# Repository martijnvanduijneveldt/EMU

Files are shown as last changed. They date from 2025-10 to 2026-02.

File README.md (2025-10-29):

[][cc-by-nc-sa]

# EMU – Expandable Multi-material Unit
### A new take on a MMU by <a href="https://github.com/DW-Tas">DW-Tas</a> and <a href="https://github.com/igiannakas">igiannakas</a><br/>
<a href="https://ko-fi.com/O5O5OCC0K"> Ko-Fi</a>

> [!WARNING] 
> ***Under Active/Early Development*** <br/>
> Build at your own risk

**Introducing the EMU, the Expandable Multi-material Unit from down under.** The EMU is a modular, flexible, upgradable, reliable and service-friendly MMU designed around the proven filamentalist V3 platform.

The EMU supports any number of lanes and base configurations; whether it is a **single lane setup** to assist filament loading, a **dual lane configuration** for endless spool, or a **multi-lane, multi base unit setup** for multi-material printing. It is also **expandable**, with no re-printing of parts required when upgrading from a 2 lane to a multiple lane setup.

<p align="center">
  
</p>

### Table of Contents
- [Design Objectives & Key Features](#design-objectives)
- [Render Gallery](#render-gallery)
- [Prints Gallery](#prints-gallery)
- [Documentation](/docs)
  - [BOM, Printing, Assembly and Wiring instructions](/docs/assembly_wiring)
  - [Software Setup and Calibration](/docs/software_setup)
  - [Slicer setup and optimisation for multi color prints](/docs/software_setup/05-slicer-setup.md)
- [License](#this-work-is-licensed-under-a)

### Highlights
- **Modular & Expandable** design, able to add lanes anytime and in any configuration. No reprints when upgrading from a 2 lane setup.
- **One screw or tool-free** access and servicing, even mid-print.
- **Sealed dry boxes** able to maintain humidity in the 15% range (with silica gel) or 5–8% range (with molecular sieves) for weeks.  
- **Humidity sensors** per lane for filament environmental monitoring.
- **Reliable endless spool** with no chance of the rewound filament interfering with neighbouring rolls.
- **Off-the-shelf electronics** (EBB42 with EBB36 also fully compatible).  
- **Per-lane controls** - eject button + LEDs.

<p align="center">
  
  
</p>

## Design Objectives

### Modularity & Upgradeability  
Each lane is fully self-contained, so you can choose **exactly how many lanes you need and group them as you like**. You can also **mix and match** lanes across multiple base units, or use a stand-alone single lane for extruder loading and print assistance. 

Expanding later is also straightforward. Just print lane expanders for the base and add another dry box assembly. There is no need to reprint or replace existing parts when upgrading from a 2 lane base. 

### Ease of Servicing 
All electrical and mechanical components are either **one screw or completely tool-free and immediately accessible**, making live troubleshooting possible even during a print. 

Access to the electronics is easy - just lift the dry box off its base for full access. The stepper tensioning screw is accessible without any dissassembly allowing on the fly tuning of filament grip. Finally, removing the filamentalist, stepper and stepper assembly is possible via one screw.

### Sealed Dry Boxes  
Each spool sits in its own purpose built, **fully sealed dry box with an integrated desiccant holder**. The boxes use foam cord in areas of potential air ingress to create a tight seal, with the clear 1.5mm PETG/PC panel also offering visibility inside the dry box.

The dry boxes can maintain humidity in the 15% range (with silica gel) or 5–8% range (with molecular sieves) for weeks. Finally, as each dry box is self contained, opening one to reload filament, doesn’t disturb its neighbours, extending the effective desiccant life.

<p align="center">
  
</p>

### Integrated Humidity Sensors 
Each lane monitors its own environment, letting you know when it’s **time to refresh the desiccant**. The humidity sensors are integrated into Mainsail (and optionally in Home Assistant for historical data tracking via the mainsail HA integration).

### Endless Spool Reliability
Dual pre-stepper sensors ensure **consistent run-out detection** and reliable re-wind, as the filament is always gripped by the stepper hobbed gear assembly. 

In addition, the isolated boxes ensure that any left over, rewound, filament cannot interfere with neighbouring lanes, **preventing a jam**.

### Built on the Filamentalist
The lane assembly is based on the proven **[filamentalist V3 design with 688 bearings](https://github.com/Enraged-Rabbit-Community/ERCF_v2/tree/master/Recommended_Options/Filamentalist_Rewinder/Filamentalist_FV3_Rewinder)**, with no modifications necessary. 
- Existing 688 bearing version filamentalist parts can be reused when building an EMU.
- Optionally, the revised tensioner mount further improves pre-stepper switch actuation.
- Wide spool size compatibility - built on the 74mm filamentalist stock setup and fits even KVP filament spools.

<p align="center">
  
  
</p>

### Integrated Filament Driving Stepper 
Each lane has its own driving stepper inside the dry box, resulting in a compact, **fully self-contained mechanical design**. In case of mechanical issue, you can swap out filamentalist assemblies with 3 screws, unplugging 2 JST plugs and unplugging the bowden tube. 

In addition, you can **swap out complete dry boxes** by unplugging two JST plugs and the bowden tube. This is helpful if you want to maintain a particularly moisture sensitive filament undisturbed when swapping it out from the EMU.

### Simple Electronics
The recommended BOM uses **readily available EBB42 boards** (with EBB36 fully compatible). MMB v2 boards can also be reused, though without humidity sensing due to I²C limitations and a slightly more intricate wiring.

In addition, **each lane has its own ventilation fan**, ensuring the stepper drivers do not overheat, even when the unit is placed on top of a hot printer. With the EBB42 and EBB36, the ventilation fans can also be speed controlled to minimize noise.

### Easy mounting
The EMU base assembly can be securely **mounted on extrusions** or using **rubber feet** directly on the printer or besides it. In either case the **electronics remain accessible** without needing to remove the unit from its mounts.

### Per-lane Controls  
Each lane includes its own eject button, status LED, and a filament colour LED that illuminates the dry box. 

## Render Gallery
<p align="center">
  
  
</p>
<p align="center">
  
  
</p>
<br/>

## Prints Gallery
<p align="center">
  1 (4)
  1 (5)
  1 (2)
  1 (3)
</p>

## This work is licensed under a
[Creative Commons Attribution-NonCommercial-ShareAlike 4.0 International License][cc-by-nc-sa].

[][cc-by-nc-sa]

[cc-by-nc-sa]: http://creativecommons.org/licenses/by-nc-sa/4.0/
[cc-by-nc-sa-image]: https://licensebuttons.net/l/by-nc-sa/4.0/88x31.png
[cc-by-nc-sa-shield]: https://img.shields.io/badge/License-CC%20BY--NC--SA%204.0-lightgrey.svg

## License clarification regarding non-commercial use:
The non-commercial aspect of this license is for cases where EMU is the product, not the use of EMU to create products.<br/>
I.e. If you wish to sell EMU as a product, you would need to seek a commercial license before doing so. </br>
It is NOT intended to prevent the use of EMU with a printer that you use to provide commercial services. If you want to run EMU in your print farm, go right ahead.

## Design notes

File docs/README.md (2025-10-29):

[][cc-by-nc-sa]

# EMU – Expandable Multi-material Unit Documentation
### A new take on a MMU by <a href="https://github.com/DW-Tas">DW-Tas</a> and <a href="https://github.com/igiannakas">igiannakas</a><br/>
<a href="https://ko-fi.com/O5O5OCC0K"> Ko-Fi</a>

## Step 1: [Printing, assembly and wiring](/docs/assembly_wiring)
This page explains the EMU assembly and wiring. It links the BOM, detailed print settings for all of the EMU parts, including tips on how to achieve the optimal print reseults. It also includes the assembly videos, covers multi-lane and single-lane wiring for both EBB42/36 boards.

- [BOM](/docs/assembly_wiring/#bom)
- [Print Settings](/docs/assembly_wiring/#print-settings)
  - [Filamentalist components and Lane stepper components](/docs/assembly_wiring/#filamentalist-components-and-lane-stepper-components)
  - [Dry Box components](/docs/assembly_wiring/#dry-box-components)
  - [Base unit components](/docs/assembly_wiring/#base-unit-components)
- [Assembly Videos](/docs/assembly_wiring/#assembly-videos)
  - [Part 1: Filamentalist and Stepper Assembly Guide](/docs/assembly_wiring/#part-1-filamentalist-and-stepper-assembly-guide)
  - [Part 2: Drybox Assembly Guide](/docs/assembly_wiring/#part-2-drybox-assembly-guide)
  - [Part 3: Base Assembly Guide](/docs/assembly_wiring/#part-3-base-assembly-guide)
  - [Part 4: Electronics Assembly Guide](/docs/assembly_wiring/#part-3-base-assembly-guide)
- [Wiring Instructions and Diagrams](/docs/assembly_wiring/#wiring-instructions-and-diagrams)

## Step 2: [EMU board setup](/docs/software_setup/01-board-setup.md)
This page explains in detail how to setup your EMU boards with CANBus, how to flash Katapult and klipper as well as the procedure to update the klipper firmware.

- [Setting up CAN Bus](/docs/software_setup/01-board-setup.md#setting-up-can-bus)
- [Flashing the EBB boards](/docs/software_setup/01-board-setup.md#flashing-the-ebb-boards)
- [Updating the boards with the latest klipper version](/docs/software_setup/01-board-setup.md#updating-the-boards-with-the-latest-klipper-version)

## Step 3: [Happy Hare setup](/docs/software_setup/02-happy-hare-setup.md)
This page explains the step by step process to install and set up Happy Hare, the MMU management software that drives the EMU.

- [Installing Happy Hare](/docs/software_setup/02-happy-hare-setup.md#installing-happy-hare)
- [Configuring the EMU hardware](/docs/software_setup/02-happy-hare-setup.md#configuring-the-emu-hardware)
- [Configuring Happy Hare parameters](/docs/software_setup/02-happy-hare-setup.md#configuring-happy-hare-parameters)
      
## Step 4: [Calibration and startup](/docs/software_setup/03-calibration-and-startup.md)
This page explains the step by step process to calibrate the unit and the initial start up checks required to ensure successful first operation.

- [Lane rotation distance calibration](/docs/software_setup/03-calibration-and-startup.md#lane-rotation-distance-calibration)
- [Bowden tube calibration](/docs/software_setup/03-calibration-and-startup.md#bowden-tube-calibration)
- [First start up](/docs/software_setup/03-calibration-and-startup.md#first-start-up)

## Step 5: [Slicer setup and optimisation for multi color prints](/docs/software_setup/05-slicer-setup.md)
Describes the mangatory Orca slicer setup required for single extruder multi-material printing, including print profile settings to achieve optimal quality results.

- [Orca slicer mandatory setup](/docs/software_setup/05-slicer-setup.md#orca-slicer-mandatory-setup)
- [Orca slicer profile tuning for multi-color printing](/docs/software_setup/05-slicer-setup.md#orca-slicer-profile-tuning-for-multi-color-printing)

## Next steps
Once you have completed the guide above you should have a fully functioning EMU unit! Optionally you can also set up:
1. Klipper screen integration: https://github.com/moggieuk/Happy-Hare/wiki/KlipperScreen
2. Mainsail / Fluid MMU panel: https://github.com/moggieuk/Happy-Hare/wiki/Mainsail-Fluidd-Integration
3. Spoolman: https://github.com/moggieuk/Happy-Hare/wiki/Spoolman-Support

In addition, to add further lanes, follow  the instructions here: [Expanding the unit](/docs/software_setup/04-expanding-the-unit.md)

## Seeking help

The Happy Hare discord is a great resource to help you going. Both in the general channel as well as the dedicated EMU channel. Link to the discord can be found here: https://discord.gg/aABQUjkZPk

<p align="center">
  
</p>

#### This work is licensed under a
[Creative Commons Attribution-NonCommercial-ShareAlike 4.0 International License][cc-by-nc-sa].

[][cc-by-nc-sa]

[cc-by-nc-sa]: http://creativecommons.org/licenses/by-nc-sa/4.0/
[cc-by-nc-sa-image]: https://licensebuttons.net/l/by-nc-sa/4.0/88x31.png
[cc-by-nc-sa-shield]: https://img.shields.io/badge/License-CC%20BY--NC--SA%204.0-lightgrey.svg

### License clarification regarding non-commercial use:
The non-commercial aspect of this license is for cases where EMU is the product, not the use of EMU to create products.<br/>
I.e. If you wish to sell EMU as a product, you would need to seek a commercial license before doing so. </br>
It is NOT intended to prevent the use of EMU with a printer that you use to provide commercial services. If you want to run EMU in your print farm, go right ahead.

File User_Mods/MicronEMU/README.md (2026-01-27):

# Micron EMU hat

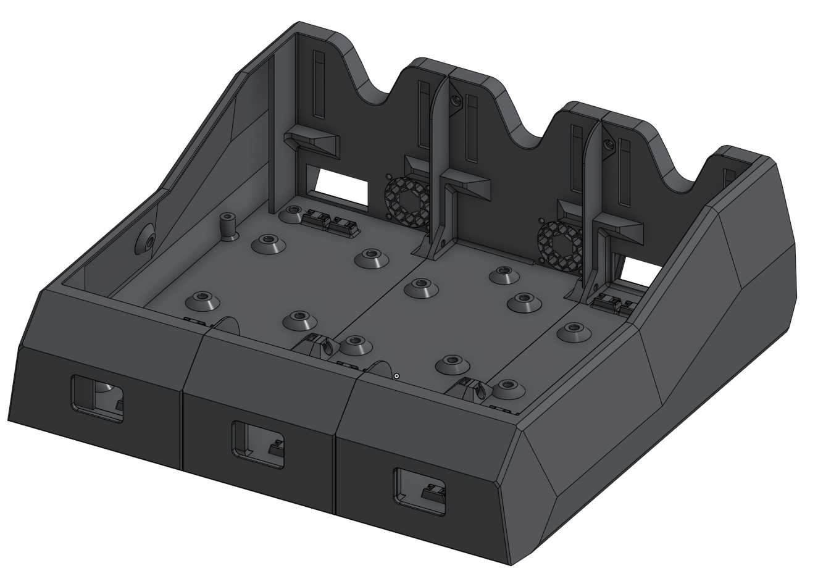
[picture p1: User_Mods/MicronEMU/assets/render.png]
a CAD render of the Micron EMU bases


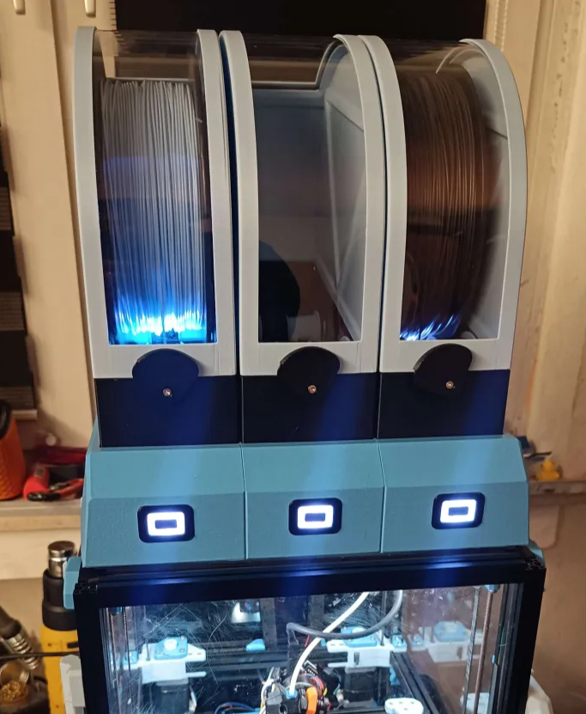
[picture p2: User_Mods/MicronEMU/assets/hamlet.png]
a photograph of the Micron EMU base in light blue on top of M.211 "Hamlet"


This mod replaces the base units to fit three boxes onto a Micron in *stealth* aesthetic. It mounts to the top extrusions using four screws, requiring post-loading of two nuts per front-to-back top extrusion.

Print using upstream settings, including painting fuzzy skin.

## Acknowledgements

Many thanks to @hartk for providing the rough-cut of the Micron EMU base. @burkfers cut the button holes, did diverse polishing, and tested.

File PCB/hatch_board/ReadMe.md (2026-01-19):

## EMU Wiring Hatch Board

The **EMU Wiring Hatch Board** is a dedicated PCB designed for EMU to make wiring and assembly easier and more convenient. It replaces the printed hatch ([Box_wiring_hatch](https://github.com/DW-Tas/EMU/blob/main/STL/Box/%5Ba%5D_Box_wiring_hatch.stl)), eliminates the need to solder the Filamentalist assembly wires to the JST connectors, and removes the need to use silicone to seal gaps around the JST connector.

The EMU Wiring Hatch Board was designed and developed by <a href="https://github.com/kashine6">kashine6</a>.

## Key Features

1. **Eliminates the need to solder wires directly to JST connectors**
   - Simplifies assembly
   - Reduces soldering complexity
   - Improves maintainability, as the Filamentalist assembly can be easily unplugged from inside the base unit

2. **Simplified pre-stepper sensor connections**
   - The two pre-stepper switches no longer need to be soldered in parallel. Instead, solder the sensor and ground wires to each switch individually, then plug them into the board separately.

3. **Easier box sealing**
   - Removes the need to use silicone to seal the JST connector on the hatch cover.

4. **Wire labeling**
   - Wire labels on the PCB silkscreen reduce the chance of wiring errors during assembly.



## BOM variations vs. baseline EMU BOM
Due to the PCB being thinner than the printed box wiring hatch, **the 2x M3x8mm FHCS screws are now replaced by 2x M3x6 BHCS/SHCS screws**.

If buying pre-assembled, the corresponding straight through hole PCB header JST connectors in the BOM are no longer needed (1x JST XH 8 pin plug and 1x JST XH 4 pin plug).

If making your own and soldering the JST headers, you'll need the below additions:
- 3x JST XH Series Straight Through Hole PCB Header, 4 Contact
- 3x JST XH Series Straight Through Hole PCB Header, 2 Contact 

## This work is licensed under a
[Creative Commons Attribution-NonCommercial-ShareAlike 4.0 International License][cc-by-nc-sa].

[][cc-by-nc-sa]

[cc-by-nc-sa]: http://creativecommons.org/licenses/by-nc-sa/4.0/
[cc-by-nc-sa-image]: https://licensebuttons.net/l/by-nc-sa/4.0/88x31.png
[cc-by-nc-sa-shield]: https://img.shields.io/badge/License-CC%20BY--NC--SA%204.0-lightgrey.svg

## License clarification regarding non-commercial use:
The non-commercial aspect of this license is for cases where EMU is the product, not the use of EMU to create products.<br/>
I.e. If you wish to sell EMU as a product, you would need to seek a commercial license before doing so. </br>
It is NOT intended to prevent the use of EMU with a printer that you use to provide commercial services. If you want to run EMU in your print farm, go right ahead.

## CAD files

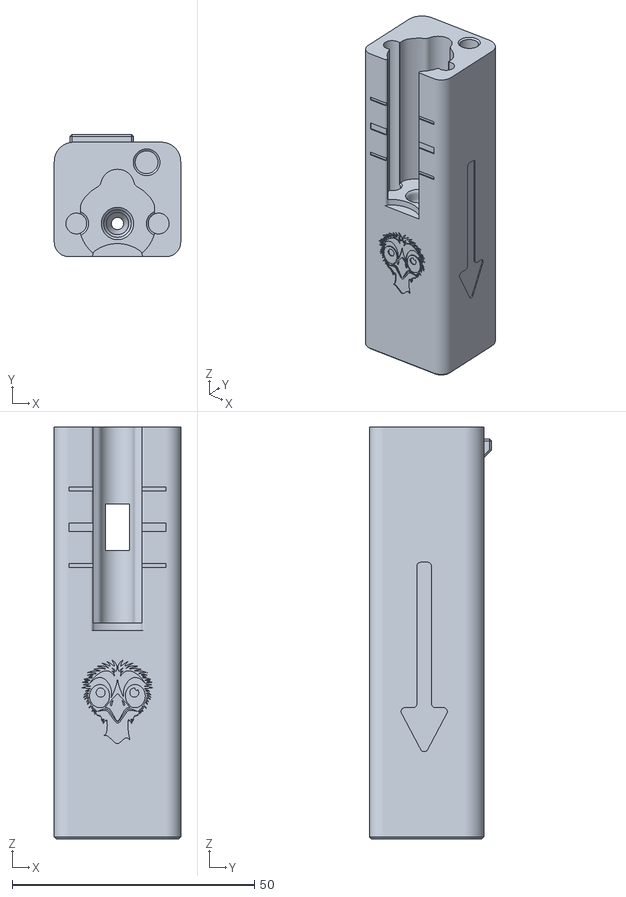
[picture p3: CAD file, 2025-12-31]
STL/Tension-compression-sensor/Proportional Sync Feedback (PSF) Version/EMUSync_main_body[PSF].stl
26.1 x 25.2 x 85.0

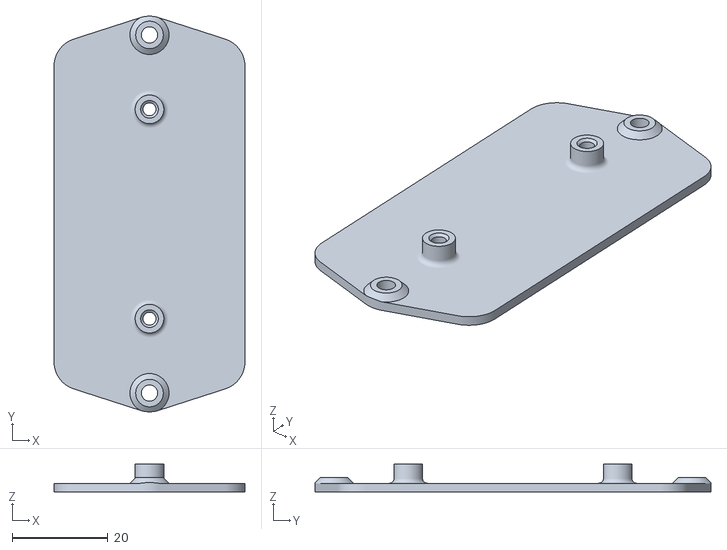
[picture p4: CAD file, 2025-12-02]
STL/Base/[a]_Ebb36_Mount.stl
40.0 x 82.9 x 5.80

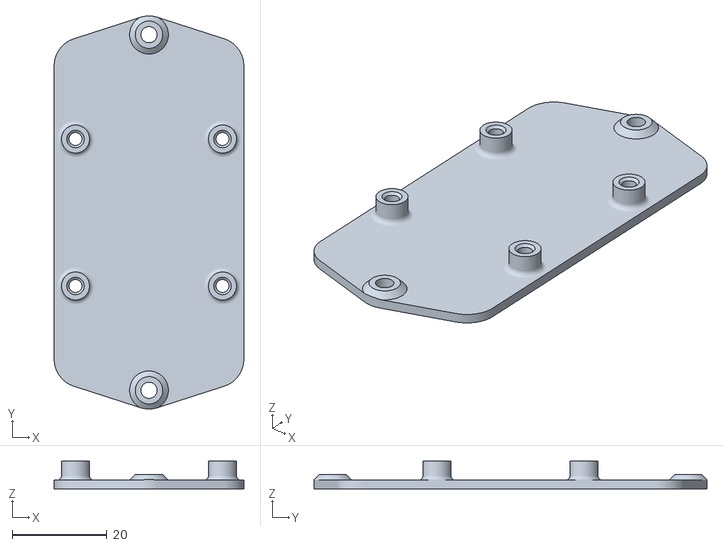
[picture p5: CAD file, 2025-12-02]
STL/Base/[a]_Ebb42_Mount.stl
40.0 x 82.9 x 5.80

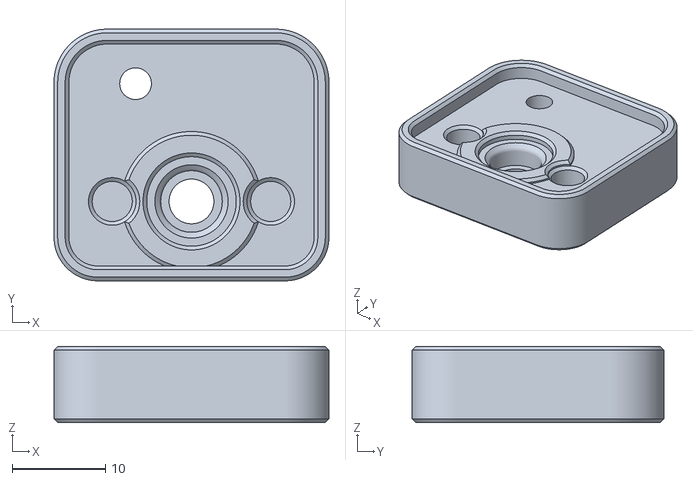
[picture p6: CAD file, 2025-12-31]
STL/Tension-compression-sensor/Proportional Sync Feedback (PSF) Version/[a]_End_cap[PSF].stl
29.5 x 27.0 x 8.20

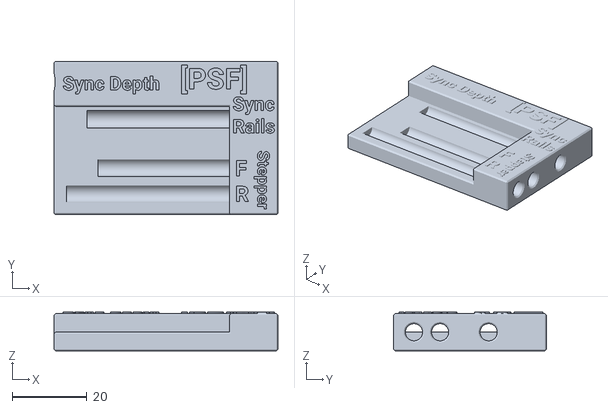
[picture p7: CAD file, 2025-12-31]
STL/Tension-compression-sensor/Proportional Sync Feedback (PSF) Version/PTFE Cutter and Length Tool[PSF].stl
60.0 x 41.0 x 10.4

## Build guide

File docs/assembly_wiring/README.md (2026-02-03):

# EMU - BOM, Printing, Assembly and Wiring Guide

## Table of Contents
- [BOM](#bom)
- [Print Settings](#print-settings)
  - [Filamentalist components and Lane stepper components](#filamentalist-components-and-lane-stepper-components)
  - [Dry Box components](#dry-box-components)
  - [Base unit components](#base-unit-components)
- [Assembly Videos](#assembly-videos)
  - [Part 1: Filamentalist and Stepper Assembly Guide](#part-1-filamentalist-and-stepper-assembly-guide)
  - [Part 2: Drybox Assembly Guide](#part-2-drybox-assembly-guide)
  - [Part 3: Base Assembly Guide](#part-3-base-assembly-guide)
  - [Part 4: Electronics Assembly Guide](#part-3-base-assembly-guide)
  - [Part 5: EMU Sync Assembly images](#part-5-emu-sync-assembly-images)
- [Wiring Instructions and Diagrams](#wiring-instructions-and-diagrams)
- [Wiring key dimensions](#wiring-key-dimensions)
  - [Base wiring dimensions](#base-wiring-dimensions)
  - [PCB Hatch wiring dimensions](#pcb-hatch-wiring-dimensions)
  - [DIY Hatch (no pcb) wiring dimensions](#diy-hatch-no-pcb-wiring-dimensions)

<p align="center">
  
</p>

## BOM  
The EMU Bill of Materials can be found here: [Draft BOM](https://docs.google.com/spreadsheets/d/1jYJXBgpc_iLDfC17fC2LTYKrSEy5ocPbGEQ_EEOGCvI)

**Recommended optional extras:**
1. [PCB hatch boards](https://github.com/DW-Tas/EMU/tree/main/PCB/hatch_board) - simplifies wiring.
2. [Proportional Sync Feedback Sensor](https://www.aliexpress.com/item/1005010470743517.html) - allows for clog, tangle detection and more accurate syncronisation between the EMU and the extruder.

## Print Settings

### Filamentalist components and Lane stepper components:
The below print settings are recommended for the filamentalist and lane stepper components. These are structural parts hence require print settings optimised for strength:
- 0.2 mm layer height
- 0.2 mm first layer height
- 4 walls
- 40% infill
- 0.4mm extrusion width (line width) throughout
- Gyroid sparse infill is recommended as it tends to warp less
- Inner Outer wall ordering, to ensure overhangs and supported areas do not sag
- Arachne wall generator
- One wall top and bottom surfaces (optional but recommended - parts look nicer)
- Disable thick bridges
- Z hop enabled to avoid nozzle scraping (0.2 is sufficient)

> [!IMPORTANT]
> **Parts are not shrinkage compensated** - calibrate your filament shrinkage first! If the bearings are loose, you're either under extruding, or over compensating for shrinkage.<br/>
> **Disable thick bridges** in your slicer and make sure your flow rate (EM) is on point! **Over extrusion, thick bridges and insufficient cooling will cause your sensor magnets and bearings not to fit as the bridges will sag.**

**For the TPU filamentalist CDR ring:**
- 0.2 mm layer height
- 0.2 mm first layer height
- 0.4mm extrusion width (line width) throughout
- 6 walls, so that the object is printed solid
- Avoid crossing walls enabled
- Random seam. This is important to avoid an aligned seam bump
- Inner Outer wall ordering, to ensure overhangs and supported areas do not sag
- Z Hop turned off to reduce stringing
  
> [!IMPORTANT]
> Printing TPU can be a challenge - print by object and a slight negative (-0.1) extra length on retract can help reduce stringing.

### Dry Box components:
The below print settings are recommended for the dry boxes and the desiccant holder. The dry boxes need to be as air tight as possible, hence the recommended print settings below are tuned to achieve this while keeping filament use under control.
- 0.2 mm layer height
- 0.2 mm first layer height
- 3 walls
- 15% infill
- For the lid specifically, use 4 walls and 30% infill to ensure strength in the front lip.
- 0.4mm extrusion width (line width) throughout
- Gyroid sparse infill is recommended as it tends to warp less
- Inner Outer wall ordering, to ensure dry box hatch features print with minimal sagging.
- Arachne wall generator
- One wall top and bottom surfaces (optional but recommended - parts look nicer)
- Disable thick bridges
- Z hop enabled to avoid nozzle scraping (0.2 is sufficient)

> [!IMPORTANT]
> Print with **extra first layer squish, use an adhesion promoter on the bed and in a pre-heated chamber with low fan** to prevent warping and ensure better layer adhesion. Mouse ears on the box corners may be required. Slight lifting will not impact part function.<br/>
> **Do not use mouse ears on the lid** as the slicer wrongly fills in the aesthetic lines.<br/>
> **Over extrude (only) the box and lid by ~2% (0.02)** to ensure air tightness. Increase your slicer flow multiplier (EM) by 0.02.

### Base unit components:
The below print settings are recommended for the base units and their accessories. 
- 0.2 mm layer height
- 0.2 mm first layer height
- 3 walls
- 15% infill
- 0.4mm extrusion width (line width) throughout
- Gyroid sparse infill is recommended as it tends to warp less
- Inner Outer Inner wall ordering to improve visual appearance
- Arachne wall generator
- One wall top and bottom surfaces (optional but recommended - parts look nicer)
- Disable thick bridges
- Z hop enabled to avoid nozzle scraping (0.2 is sufficient)
- For the **Eject button lens, 99 walls are recommended,** to reduce possibility of infill shining through the natural ABS

> [!IMPORTANT]
> Print with **extra first layer squish, use an adhesion promoter on the bed and in a pre-heated chamber with low fan** to prevent warping. Slight lifting will not impact part function.

> [!NOTE]
> **Paint on fuzzy skin** on the outer walls of the base unit will improve appearance.<br/>
> Paint on ONLY, not full model fuzzy skin. <br/>
> 0.1 distance, 0.1 or 0.2mm depth. Displacement method (orca slicer)

## Assembly Videos

### Part 1: Filamentalist and Stepper Assembly Guide
EMU Filamentalist and Stepper Assembly Guide (https://www.youtube.com/watch?v=FNcXC9HXUmI)
<br/>
**Errata:**
1. BMG Gear insertion is not visible in the video. Do this before adding the stepper main body and screwing it on.
2. Switch sensor screws are M2x10 self taping or m2x8 bhcs/shcs
3. Filament path - BMG gear alignment step is not shown in the video. Insert some filament through the unit manually, loosen the BMG gear set screw and move it back and forth. Screw down the BMG gear.
4. For the BMG tensioning arm, the bushing is no longer an option. 
5. Add a washer to the stepper tensioning arm on both sides of the spring.
6. Stepper body screws are all M3x20
7. Front ECAS is no longer required
8. PTFE tube lengths have been updated since the video release. [Use the dedicated cutter STL](https://github.com/DW-Tas/EMU/blob/main/STL/Tools/PTFE%20Cutter%20and%20Length%20Tool.stl) to measure and cut the PTFE tubes.

### Part 2: Drybox Assembly Guide
EMU Dry Box Assembly Guide (https://www.youtube.com/watch?v=JZzMyOBCdSM)
<br/>

**Errata:**
1. A threaded stand off is inserted in the front lip of the lid and secured from either side with M3x40 FHCS bolts.
2. Box and wiring hatch changes - the wiring hatch now is screwed in from the outside of the unit. Push through the hole from the inside out and then screw in place.
3. Wiring hatch foam is now glued on the box itself. The foam chord channel is on the outside of the box. 
4. The BME sensor has been relocated to the LED cover.

### Part 3: Base Assembly Guide
EMU Base Assembly Guide (https://www.youtube.com/watch?v=2SmAMuXas38)
<br/>

### Part 4: Electronics Assembly Guide
EMU Elecrronics Assembly Guide (https://www.youtube.com/watch?v=Iang2JYkTh8)
<br/>

**Errata:**
1. Base unit top clamping screws (M3x8 FHCS) now screw into heatset inserts inserted on the other side of the frame.
2. External combiner sensor is no longer specified in the default setup. That wiring part can be omitted.
3. Encoder is no longer specified in the default setup. That wiring part can be omitted.

### Part 5: EMU Sync Assembly images
<table>
  <tr>
    <td>Step 1</td>
    <td>Step 2</td>
    <td>Step 3</td>
  </tr>
  <tr>
    <td>Step 4</td>
    <td>Step 5</td>
    <td>Step 6</td>
  </tr>
  <tr>
    <td>Step 7</td>
    <td>Step 8</td>
    <td>Step 9</td>
  </tr>
  <tr>
    <td>Step 10</td>
    <td>Step 11</td>
    <td>Step 12</td>
  </tr>
  <tr>
    <td>Step 13</td>
    <td>Step 14</td>
    <td>Step 15</td>
  </tr>
</table>

### Combiner:
Make sure the PTFE tube is pushed all the way inside the combiner. Not just at the ecas entry!



## Wiring Instructions and Diagrams
Depending on the number of lanes assembled, the wiring will vary slightly. Below are some initial wiring key notes to get your started.<br/>

**Multi-lane setup wiring notes (2+ lanes)**
1. Please note that the sync feedback sensor is connected to the first lane board. The encoder and combiner endstop is connected to the second lane EBB board.
2. The CAN bus umbilical from the printer feeds power and the CAN H / L wires to the WAGO connectors in the first lane. 
3. A 24V and Ground "bus" is established throughout the base unit using the two rearward WAGO connectors (WAGO 3 and WAGO 4).
4. The EBB boards connect to the power bus for power via their XT ports.
5. The EBB boards are daisy chained to establish the CANbus network. The first lane canbus High / Low / Power wires are connected to the first lane WAGO connectors.
7. The second lane canbus High / Low wires are connected to the CAN out dupont connectors on the first board itself. Creates the daisy chain
9. The last EBB board needs the 120Ohm resistor installed.
10. The second lane, third lane etc 2nd WAGO connector is used to connect the Neopixel Out wire from the eject button to the Neopixel In wire on the dry box.
11. The second lane, third lane etc 1st WAGO connector is used to connect the Neopixel Out wire from the dry box to the next lane Neopixel In wire on the eject button.

**Adding a second base unit** <br/>
You can daisy chain as many base units as you desire. Simply wire the XT30+2 CAN out port next to the last lane to the power bus and CAN H / L dupont connectors on the last EBB board. The next base unit can connect using a standard CAN Bus cable to the first unit.

**Single-lane setup wiring notes (2+ lanes)** <br/>
1. A single lane setup does not support an encoder/combiner. Instead, the Post Extruder sensor is configured in the Happy Hare configuration as the gate sensor.
2. There is no daisy chaining required. The single EBB board is connected to the first lane WAGO connectors.
3. There is no daisy chaining of subsequent lane Neopixels. 

**EBB 42 wiring diagram**<br/>
<p align="center">
  
</p>

**EBB 36 wiring diagram**<br/>
Please note, the EBB36 uses identical pin definitions to the EBB42.
<p align="center">
  
</p>

**Printer PSU**<br/>
> [!WARNING]
> You need to evaluate whether your PSU has enough power headroom. This entirely depends on your printer's overall setup. Ideally **plan for ~20 Watts for an 5 lane MMU** with **each additional lane requiring approximately an additional ~2-2.5 Watts.**

Key factors to consider:
1. PSU wattage
2. How many A-B/X-Y and Z steppers 
3. At what current the main printer steppers are operating at and what print speeds you operate them at
4. Your heater cartridge wattage 
5. What other power consuming accessories are connected to the printer (cpap, heater bed if 24V etc)

Depending on the combined power consumption, you may need to consider whether a PSU upgrade is needed. 

As a rule of thumb, a 12 lane EMU build with 4 Z steppers and 2 AB steppers running moderately high currents and high print speeds on a Voron 2.4 may require a 350Watt power supply to ensure adequate power headroom.

## Wiring key dimensions

This parts describes the recommended wire length for easy assembly and maintenance.

### Base wiring dimensions

<p align="center">
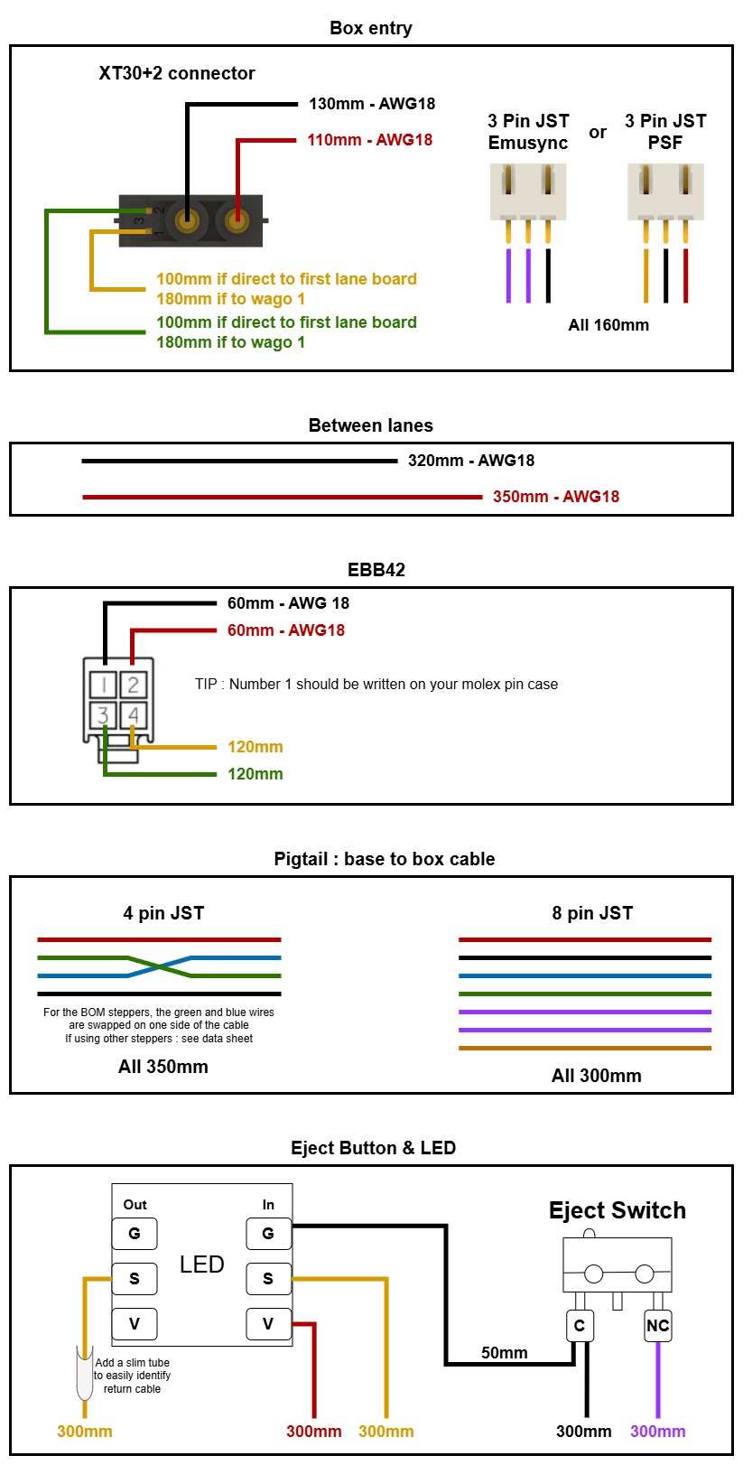
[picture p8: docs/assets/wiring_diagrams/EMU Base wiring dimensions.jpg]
  
</p>

### PCB Hatch wiring dimensions
> These dimensions are for the latest version of the PCB (Post sensor at the rear). If you have the older board (Post Sensor at the center) [refer to this image](../assets/wiring_diagrams/EMU%20PCB%20Hatch%20wiring%20dimensions%20-%20Old%20PCB.jpg) for sensor wire lengths.
<p align="center">
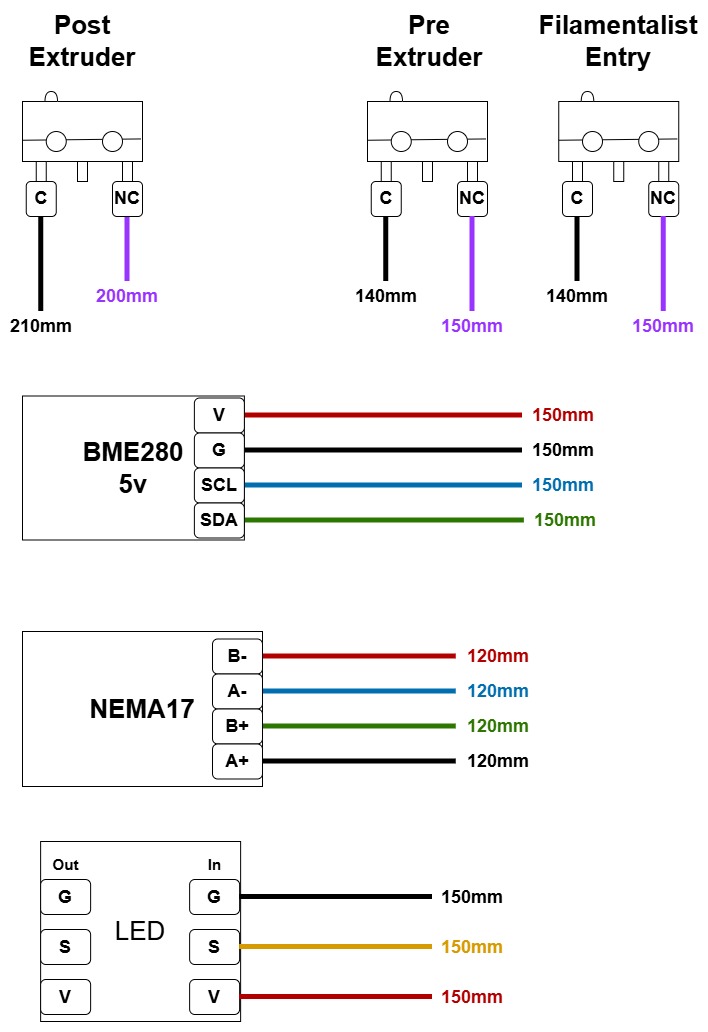
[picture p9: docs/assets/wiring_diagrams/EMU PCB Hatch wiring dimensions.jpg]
  
</p>

### DIY Hatch (no pcb) wiring dimensions

> These wiring dimensions assume you mount the BME sensor on the led cover and connect `5V` and `Ground` of the BME sensor to the led out `5V` and `Ground`.

<p align="center">
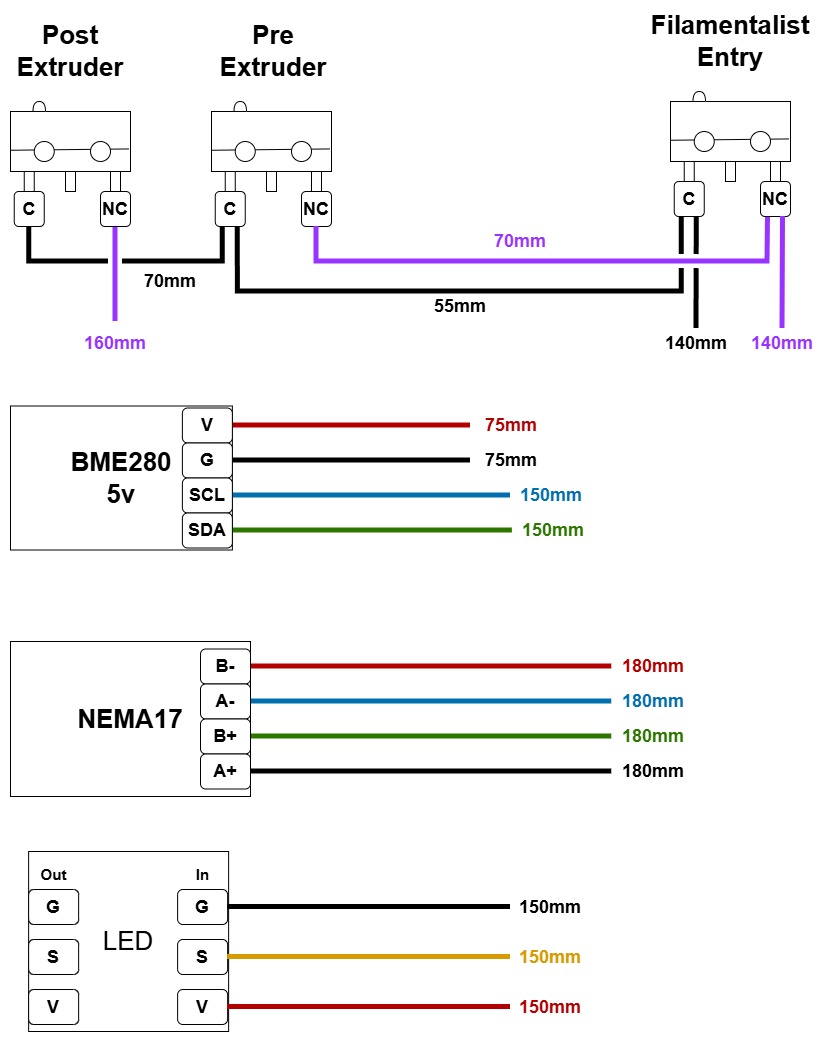
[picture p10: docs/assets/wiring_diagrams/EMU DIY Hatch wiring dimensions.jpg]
  
</p>

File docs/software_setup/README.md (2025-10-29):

# EMU Software Setup Guide

This is a provisional sofware setup guide for the EMU using Happy Hare v3. Happy Hare is an open-source filament changer controller for multi-color printing and is required for the EMU to function.

This guide is meant to be read in conjunction with the Happy Hare guides as found here: https://github.com/moggieuk/Happy-Hare/wiki and with Esoterical's CANBus setup guide as found here: https://canbus.esoterical.online. 

## Table of Contents

- [EMU board setup guide](/docs/software_setup/01-board-setup.md)
  - [Setting up CAN Bus](/docs/software_setup/01-board-setup.md#setting-up-can-bus)
  - [Flashing the EBB boards](/docs/software_setup/01-board-setup.md#flashing-the-ebb-boards)
  - [Updating the boards with the latest klipper version](/docs/software_setup/01-board-setup.md#updating-the-boards-with-the-latest-klipper-version)
- [Happy Hare setup guide](/docs/software_setup/02-happy-hare-setup.md)
  - [Installing Happy Hare](/docs/software_setup/02-happy-hare-setup.md#installing-happy-hare)
  - [Configuring the EMU hardware](/docs/software_setup/02-happy-hare-setup.md#configuring-the-emu-hardware)
  - [Configuring Happy Hare parameters](/docs/software_setup/02-happy-hare-setup.md#configuring-happy-hare-parameters)
- [Calibration and startup guide](/docs/software_setup/03-calibration-and-startup.md)
  - [Lane rotation distance calibration](/docs/software_setup/03-calibration-and-startup.md#lane-rotation-distance-calibration)
  - [Bowden tube calibration](/docs/software_setup/03-calibration-and-startup.md#bowden-tube-calibration)
  - [First start up](/docs/software_setup/03-calibration-and-startup.md#first-start-up)
- [Expanding the unit guide](/docs/software_setup/04-expanding-the-unit.md)
- [Slicer setup and optimisation for multi color prints](/docs/software_setup/05-slicer-setup.md)
  - [Orca slicer mandatory setup](/docs/software_setup/05-slicer-setup.md#orca-slicer-mandatory-setup)
  - [Orca slicer profile tuning for multi-color printing](/docs/software_setup/05-slicer-setup.md#orca-slicer-profile-tuning-for-multi-color-printing)

## Next Steps
Once you have completed the guide above you should have a fully functioning EMU unit! Optionally you can also set up:
1. Klipper screen integration: https://github.com/moggieuk/Happy-Hare/wiki/KlipperScreen
2. Mainsail / Fluid MMU panel: https://github.com/moggieuk/Happy-Hare/wiki/Mainsail-Fluidd-Integration
3. Spoolman: https://github.com/moggieuk/Happy-Hare/wiki/Spoolman-Support

## Seeking help

The Happy Hare discord is a great resource to help you going. Both in the general channel as well as the dedicated EMU channel. Link to the discord can be found here: https://discord.gg/aABQUjkZPk

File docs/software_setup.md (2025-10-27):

# EMU Happy Hare Hardware and Software Setup Guide

This is a provisional sofware setup guide for the EMU using Happy Hare v3. This guide is meant to be read in conjunction with the Happy Hare setup guide as found here: https://github.com/moggieuk/Happy-Hare/wiki

## Table of Contents

- [Setting up CAN Bus](#setting-up-can-bus)
- [Flashing the EBB boards](#flashing-the-ebb-boards)
- [Updating the boards with the latest klipper version](#updating-the-boards-with-the-latest-klipper-version)
- [Setting up Happy Hare](#setting-up-happy-hare)
- [Configuring the EMU hardware in Happy Hare](#configuring-the-emu-hardware-in-happy-hare)
- [Configuring Happy Hare](#configuring-happy-hare)
- [Calibrating the unit](#calibrating-the-unit)
- [First start up](#first-start-up)
- [Next steps](#next-steps)

## Setting up CAN Bus
If your printer does not have canbus set up, follow the excellent guide from Esoterical here: https://canbus.esoterical.online. If you are not familiar with CAN Bus, read through the guide from Esoterical. **CAN Bus is simple to set up and operate, but please do read the guide to familiarise yourselves with the CAN Bus concepts and terminology.**

Do not forget to terminate the last EBB board or CANBus device in your bus (depending on your bus topology).

## Flashing the EBB boards
Prior to setting up the EMU, the EBB boards need to be flashed with Katapult and Klipper. Flashing instructions can be found here https://canbus.esoterical.online/toolhead_flashing.html. The boards are flashed in exactly the same way as if they were used as a toolhead board. Below are some high level instructions; however do refer back to the guide by Esoterical for a more comprehensive guide.<br/>

**Step 1:** Install katapult:<br/>
Katapult is a piece of software that sits on the EBB units (and any CAN Bus device) and acts as an easy way to set your board in "flashing mode" making klipper updates super easy. It is highly recommended that Katapult is flashed on the boards.
```
test -e ~/katapult && (cd ~/katapult && git pull) || (cd ~ && git clone https://github.com/Arksine/katapult) ; cd ~
```
**Step 2:** Connect your first EBB board over USB **outside the EMU**. Make sure the **power by USB jumper is set**.<br/>
**Step 3:** Set the board in DFU mode by pressing and holding the reset and boot buttons. Release the reset button first, then release the boot button<br/>
**Step 4:** The board should show as in DFU mode. Run ```lsusb``` and check that something like the below is shown in the command line:<br/>
```
Bus 001 Device 005: ID 0483:df11 STMicroelectronics STM Device in DFU Mode
```
**Step 5:** initiate menuconfig for Katapult.<br/>
```
cd ~/katapult
make menuconfig
```


```
make
```
**Step 6:** Flash katapult to the EBB board<br/>
```
sudo dfu-util -R -a 0 -s 0x08000000:mass-erase:force:leave -D ~/katapult/out/katapult.bin -d 0483:df11
```
**Step 7:** initiate menuconfig for klipper and make the firmware<br/>
```
sudo service klipper stop
cd ~/klipper
make clean
make menuconfig
```

```
make
```
**Step 8:** Prepare to flash klipper<br/>
Now that katapult is loaded, unplug the USB cable, remove the USB power jumper (if installed) and install the EBB on the unit. Power it via the canbus pigtail.

Please note, **you can set up katapult on all the boards and install them back to the unit all at once**. However, identifying which board is which from the UID is more tricky if you have them all installed in the unit. 

You have two options to identify them.
1. Unplug the positive (red) wire from the wagos for all the boards except the one you are intending to flash klipper, Run the command from Step 9, note the UUID, flash klipper and note down the UUID you just used with the lane number in your documentation  _--or--_
2. Run the command from Step 9, pick one UUID, flash Klipper, note which board's led stopped flashing and note down the UUID you just used with the lane number in your documentation.

**Step 9:** Find the board UUID<br/>
Run the command below and note the produced UUID
```
python3 ~/katapult/scripts/flashtool.py -i can0 -q
```
**Step 10:** Flash klipper<br/>
```
python3 ~/katapult/scripts/flashtool.py -i can0 -f ~/klipper/out/klipper.bin -u youruuid
```
**Flashing the remaining boards:** <br/>

Repeat step 2 (connect via USB),3 (set in DFU mode),4 (lsusb to confirm DFU),6 (flash katapult),8 (install the board),9 (pick the UUID),10 (flash klipper) for each subsequent board. Please note that as the boards are the same you do not need to re-run the menu config and make process.

> [!IMPORTANT]
> Remember to note down the UUID - Lane values for your reference. This combination will be used later in the guide to set up Happy Hare.

## Updating the boards with the latest klipper version
```
sudo service klipper stop
cd ~/klipper
make clean
make menuconfig
make
python3 ~/katapult/scripts/flashtool.py -i can1 -u youruuid -r
python3 ~/katapult/scripts/flashtool.py -i can1 -u youruuid -f ~/klipper/out/klipper.bin
```
Repeat the last two steps for each EBB board. Note the uuid used with the lane number in your documentation. This will be used later.

## Setting up Happy Hare
Install Happy Hare. More detailed instructions can be found here: https://github.com/moggieuk/Happy-Hare/wiki/Installation
```
cd ~
git clone https://github.com/moggieuk/Happy-Hare.git
cd ~/Happy-Hare
./install.sh -i
```
**Select MMU:** Pick option 16 - Other/Custom. <br/><br/>
<p align="center">
  Installer screen: Pick option 16 - Other/Custom
</p>

**Select MMU type:** Pick option 7 - Type-B (multiple filament drive steppers) with individual post-gear sensors, No Encoder <br/><br/>
<p align="center">
  Installer screen: Pick option 7 - Type-B with individual post-gear sensors, no encoder
</p>

**Select lane number:** Type the number of lanes you have set up. In my example below it is 8. <br/><br/>
<p align="center">
  Enter number of lanes (example: 8)
</p>

**Select the board used:** Pick option 15 - Not in list / Unknown <br/><br/>
<p align="center">
  Select board: option 15 Not in list / Unknown
</p>

**LED Support:** Enable LED support <br/><br/>
<p align="center">
  Enable LED support
</p>

**Endless Spool Support:** Enable Endless Spool support <br/><br/>
<p align="center">
  Enable Endless Spool support
</p>

**Include all the MMU config files:** Include all mmu config files in the printer.cfg <br/><br/>
<p align="center">
  Include MMU config files in printer.cfg
</p>

**(Optional) Mini 12864 screen support:** If you have a Mini 12864 screen, enabe the Happy Hare screen menu <br/><br/>
<p align="center">
  Enable Happy Hare menu for Mini 12864 (optional)
</p>

**Default pause/resume macros:** Include the default pause/resume macros from Happy Hare. Once the installation is complete, make sure you disable/remove any custom pause/resume macros that you may have in your existing Klipper installation! <br/><br/>
<p align="center">
  Include default pause/resume macros from Happy Hare
</p>

**EREC support:** Decline the installation of the EREC filament cutter <br/><br/>
<p align="center">
  Decline EREC filament cutter installation
</p>

**Moonraker.conf update:** Update your moonraker.conf as below:
```
[file_manager]
enable_object_processing: True

[mmu_server]
enable_file_preprocessor: True
enable_toolchange_next_pos: True
update_spoolman_location: True
```

<br/><br/>
Baseline setup is now complete!
<br/><br/>
## Configuring the EMU hardware in Happy Hare

### Update mmu/base/mmu.cfg
The Happy hare installer generates a generic mmu.cfg file that needs re-writing for the EMU. 

**Step 1: Clear the mmu.cfg file.** <br/><br/>
Start by completely deleting the content of that file and hitting save.

**Step 2: Update mmu.cfg with the EMU mcu boards definitions** <br/><br/>
For each lane you will need a distinct mcu mmu block defining the board name and the canbus UUID as noted earlier. In the example below I am using an 8 lane configuration.
```
[mcu mmu0]
canbus_uuid: cc8f39d714ce 
canbus_interface: can0

[mcu mmu1]
canbus_uuid: c2357f5873d7 
canbus_interface: can0

[mcu mmu2]
canbus_uuid: 31fb8c95fbfd 
canbus_interface: can0

[mcu mmu3]
canbus_uuid: 8579c5130649 
canbus_interface: can0

[mcu mmu4]
canbus_uuid: 49abda4839e6
canbus_interface: can0

[mcu mmu5]
canbus_uuid: 7d42f7c43687
canbus_interface: can0

[mcu mmu6]
canbus_uuid: 3efbe46e5d5f
canbus_interface: can0

[mcu mmu7]
canbus_uuid: f050daaa5448 
canbus_interface: can0
```

**Step 3: Update mmu.cfg with the EMU mcu board pin aliases** <br/><br/>
After the board definitions, insert the board pin aliases. 

> [!IMPORTANT]
> **Important note:** The first board defines the aliases for the tension and compression sensor too, so it is different to the rest. In the example below I am using an 8 lane configuration.
```
[board_pins mmu0]
mcu: mmu0 
aliases:
    MMU_GEAR_UART=PA15,
    MMU_GEAR_STEP=PD0,
    MMU_GEAR_DIR=PD1,
    MMU_GEAR_ENABLE=PD2,
    MMU_GEAR_DIAG=,

    MMU_NEOPIXEL=PD3,
    MMU_NEOPIXEL_LOGO=,

    MMU_PRE_GATE_0=PB7,
    MMU_POST_GEAR_0=PB5,

    MMU_TENSION=PB8, # First lane has the sync feedback sensor attached to it!
    MMU_COMPRESSION=PB9, # First lane has the sync feedback sensor attached to it!

    EJECT_BUTTON_0=PB6,

[board_pins mmu1]
mcu: mmu1 
aliases:

    MMU_GEAR_UART_1=PA15,
    MMU_GEAR_STEP_1=PD0,
    MMU_GEAR_DIR_1=PD1,
    MMU_GEAR_ENABLE_1=PD2,
    MMU_GEAR_DIAG_1=,

    MMU_PRE_GATE_1=PB7,
    MMU_POST_GEAR_1=PB5,

    EJECT_BUTTON_1=PB6,

[board_pins mmu2]
mcu: mmu2 
aliases:

    MMU_GEAR_UART_2=PA15,
    MMU_GEAR_STEP_2=PD0,
    MMU_GEAR_DIR_2=PD1,
    MMU_GEAR_ENABLE_2=PD2,
    MMU_GEAR_DIAG_2=,

    MMU_PRE_GATE_2=PB7,
    MMU_POST_GEAR_2=PB5,

    EJECT_BUTTON_2=PB6,

[board_pins mmu3]
mcu: mmu3
aliases:

    MMU_GEAR_UART_3=PA15,
    MMU_GEAR_STEP_3=PD0,
    MMU_GEAR_DIR_3=PD1,
    MMU_GEAR_ENABLE_3=PD2,
    MMU_GEAR_DIAG_3=,

    MMU_PRE_GATE_3=PB7,
    MMU_POST_GEAR_3=PB5,

    EJECT_BUTTON_3=PB6,

[board_pins mmu4]
mcu: mmu4 
aliases:

    MMU_GEAR_UART_4=PA15,
    MMU_GEAR_STEP_4=PD0,
    MMU_GEAR_DIR_4=PD1,
    MMU_GEAR_ENABLE_4=PD2,
    MMU_GEAR_DIAG_4=,

    MMU_PRE_GATE_4=PB7,
    MMU_POST_GEAR_4=PB5,

    EJECT_BUTTON_4=PB6,

[board_pins mmu5]
mcu: mmu5
aliases:

    MMU_GEAR_UART_5=PA15,
    MMU_GEAR_STEP_5=PD0,
    MMU_GEAR_DIR_5=PD1,
    MMU_GEAR_ENABLE_5=PD2,
    MMU_GEAR_DIAG_5=,

    MMU_PRE_GATE_5=PB7,
    MMU_POST_GEAR_5=PB5,

    EJECT_BUTTON_5=PB6,

[board_pins mmu6]
mcu: mmu6
aliases:

    MMU_GEAR_UART_6=PA15,
    MMU_GEAR_STEP_6=PD0,
    MMU_GEAR_DIR_6=PD1,
    MMU_GEAR_ENABLE_6=PD2,
    MMU_GEAR_DIAG_6=,

    MMU_PRE_GATE_6=PB7,
    MMU_POST_GEAR_6=PB5,

    EJECT_BUTTON_6=PB6,

[board_pins mmu7]
mcu: mmu7
aliases:

    MMU_GEAR_UART_7=PA15,
    MMU_GEAR_STEP_7=PD0,
    MMU_GEAR_DIR_7=PD1,
    MMU_GEAR_ENABLE_7=PD2,
    MMU_GEAR_DIAG_7=,

    MMU_PRE_GATE_7=PB7,
    MMU_POST_GEAR_7=PB5,

    EJECT_BUTTON_7=PB6,
```
This file is now complete! 

### Update mmu/base/mmu_hardware.cfg

**Step 1: Clear the mmu_hardware.cfg file.** <br/><br/>
Start by completely deleting the content of that file and hitting save.

**Step 2: Paste the below configuration in the mmu_hardware.cfg file**<br/><br/>
The below starter setup is for an 8 lane unit. To set up a lower lane count, paste the complete content below and change the below:
1. num_gates: 8 -> to equal to the number of lanes you have
2. Delete the unecessary tmc and stepper blocks. For example if you have a 5 lane unit, delete Filament Drive Gear_5, Filament Drive Gear_6, Filament Drive Gear_7 blocks from the below.
3. Delete the uncesessary pre_gate_switch_pin sections and post_gear_switch_pin sections. For example for a 5 lane setup, remove pre_gate_switch_pin_5, pre_gate_switch_pin_6, pre_gate_switch_pin_7, post_gear_switch_pin_5, post_gear_switch_pin_6, post_gear_switch_pin_7
4. Update the LED chain_count: 16 is for 8 lanes. This needs to be equal to number of lanes x 2. So for a 5 lane setup this would be set to 10.
5. Update the LED effect exit leds: exit_leds: neopixel:mmu_leds (1,3,5,7,9,11,13,15) is for 8 lanes. For 5, this should be 1,3,5,7,9.
6. Update the LED effect entry leds: entry_leds: neopixel:mmu_leds (2,4,6,8,10,12,14,16) is for 8 lanes. For 5, this should be 2,4,6,8,10

If you have more than 8 lanes, insert accordingly additional blocks, following the patterns as illustrated in the full configuration file below.

> [!TIP]
> If during testing you see that the EMU stepper spins backwards, invert the dir_pin by adding a ! infront of it (!dir_pin).

Finally, update your toolhead sensors definition to match your setup. Here I have the extruder entry (top) sensor in my toolhead can board named EBBCan connected to pin PB6 and the toolhead sensor (post extruder) at pin PB5.
```
extruder_switch_pin: ^EBBCan: PB6
toolhead_switch_pin: ^EBBCan: PB5
```

File contents - mmu_hardware.cfg:

```
[mmu_machine]
num_gates: 8			
mmu_vendor: Other			
mmu_version: 1.0			

selector_type: VirtualSelector
variable_bowden_lengths: 1		
variable_rotation_distances: 1		
require_bowden_move: 1		
filament_always_gripped: 1	
has_bypass: 1 

# FILAMENT DRIVE GEAR STEPPER  -----------------------------------------------------------------------------------------
[tmc2209 stepper_mmu_gear]
uart_pin: mmu0:MMU_GEAR_UART
run_current: 0.8		
hold_current: 0.2	
interpolate: False
sense_resistor: 0.110	
stealthchop_threshold: 1		

[stepper_mmu_gear]
step_pin: mmu0:MMU_GEAR_STEP
dir_pin: mmu0:MMU_GEAR_DIR
enable_pin: !mmu0:MMU_GEAR_ENABLE
rotation_distance: 22.7574		
gear_ratio: 1:1			
microsteps: 32				
full_steps_per_rotation: 200		

# Filament Drive Gear_1 --------------------------
[tmc2209 stepper_mmu_gear_1]
uart_pin: mmu1:MMU_GEAR_UART_1

[stepper_mmu_gear_1]
step_pin: mmu1:MMU_GEAR_STEP_1
dir_pin: mmu1:MMU_GEAR_DIR_1
enable_pin: !mmu1:MMU_GEAR_ENABLE_1

# Filament Drive Gear_2 --------------------------
[tmc2209 stepper_mmu_gear_2]
uart_pin: mmu2:MMU_GEAR_UART_2

[stepper_mmu_gear_2]
step_pin: mmu2:MMU_GEAR_STEP_2
dir_pin: mmu2:MMU_GEAR_DIR_2
enable_pin: !mmu2:MMU_GEAR_ENABLE_2

# Filament Drive Gear_3 --------------------------
[tmc2209 stepper_mmu_gear_3]
uart_pin: mmu3:MMU_GEAR_UART_3

[stepper_mmu_gear_3]
step_pin: mmu3:MMU_GEAR_STEP_3
dir_pin: mmu3:MMU_GEAR_DIR_3
enable_pin: !mmu3:MMU_GEAR_ENABLE_3

# Filament Drive Gear_4 --------------------------
[tmc2209 stepper_mmu_gear_4]
uart_pin: mmu4:MMU_GEAR_UART_4

[stepper_mmu_gear_4]
step_pin: mmu4:MMU_GEAR_STEP_4
dir_pin: mmu4:MMU_GEAR_DIR_4
enable_pin: !mmu4:MMU_GEAR_ENABLE_4

# Filament Drive Gear_5 --------------------------
[tmc2209 stepper_mmu_gear_5]
uart_pin: mmu5:MMU_GEAR_UART_5

[stepper_mmu_gear_5]
step_pin: mmu5:MMU_GEAR_STEP_5
dir_pin: mmu5:MMU_GEAR_DIR_5
enable_pin: !mmu5:MMU_GEAR_ENABLE_5

# Filament Drive Gear_6 --------------------------
[tmc2209 stepper_mmu_gear_6]
uart_pin: mmu6:MMU_GEAR_UART_6

[stepper_mmu_gear_6]
step_pin: mmu6:MMU_GEAR_STEP_6
dir_pin: mmu6:MMU_GEAR_DIR_6
enable_pin: !mmu6:MMU_GEAR_ENABLE_6

# Filament Drive Gear_7 --------------------------
[tmc2209 stepper_mmu_gear_7]
uart_pin: mmu7:MMU_GEAR_UART_7

[stepper_mmu_gear_7]
step_pin: mmu7:MMU_GEAR_STEP_7
dir_pin: mmu7:MMU_GEAR_DIR_7
enable_pin: !mmu7:MMU_GEAR_ENABLE_7

[mmu_sensors]
pre_gate_switch_pin_0: ^mmu0:MMU_PRE_GATE_0
pre_gate_switch_pin_1: ^mmu1:MMU_PRE_GATE_1
pre_gate_switch_pin_2: ^mmu2:MMU_PRE_GATE_2
pre_gate_switch_pin_3: ^mmu3:MMU_PRE_GATE_3
pre_gate_switch_pin_4: ^mmu4:MMU_PRE_GATE_4
pre_gate_switch_pin_5: ^mmu5:MMU_PRE_GATE_5
pre_gate_switch_pin_6: ^mmu6:MMU_PRE_GATE_6
pre_gate_switch_pin_7: ^mmu7:MMU_PRE_GATE_7

post_gear_switch_pin_0: ^mmu0:MMU_POST_GEAR_0
post_gear_switch_pin_1: ^mmu1:MMU_POST_GEAR_1
post_gear_switch_pin_2: ^mmu2:MMU_POST_GEAR_2
post_gear_switch_pin_3: ^mmu3:MMU_POST_GEAR_3
post_gear_switch_pin_4: ^mmu4:MMU_POST_GEAR_4
post_gear_switch_pin_5: ^mmu5:MMU_POST_GEAR_5
post_gear_switch_pin_6: ^mmu6:MMU_POST_GEAR_6
post_gear_switch_pin_7: ^mmu7:MMU_POST_GEAR_7

extruder_switch_pin: ^EBBCan: PB6
toolhead_switch_pin: ^EBBCan: PB5

sync_feedback_tension_pin: ^mmu0:MMU_TENSION         # Compression is when you pull the bowden tubes (entry/exit) away from each other. Tension when you push the tubes together.
sync_feedback_compression_pin: ^mmu0:MMU_COMPRESSION

# MMU NEOPIXEL LED SUPPORT ------------------------------------------------------------------------------------

[neopixel mmu_leds]
pin: mmu0:MMU_NEOPIXEL
chain_count: 16			# Number lanes x2
color_order: GRBW		# Set based on your particular neopixel specification

# MMU LED EFFECT SEGMENTS ----------------------------------------------------------------------------------------------

[mmu_leds unit0]
exit_leds:   neopixel:mmu_leds (1,3,5,7,9,11,13,15) # First, third, fifth LED and so forth.
entry_leds: neopixel:mmu_leds (2,4,6,8,10,12,14,16) # Second, fourth, sixth LED and so forth.
logo_leds:    
frame_rate: 24

enabled: True                           # LEDs are enabled at startup
animation: True                         # Use led-animation-effects
exit_effect: gate_status                # gate_status in the eject buttons
entry_effect: filament_color            # filament_color in the dry box LED
status_effect: off                      # no status LED is on the unit
logo_effect: (0, 0, 0)                  # no Logo LED is on the unit
white_light: (1, 1, 1)                  # RGB color for static white light
black_light: (1, 1, 1)                  # RGB color used to represent "black" filament
empty_light: (0.0, 0.0, 0.0)            # Empty gate has eject button "off"

effect_loading:            mmu_blue_clockwise_slow, (0, 0, 0.4)
effect_loading_extruder:   mmu_blue_clockwise_fast, (0, 0, 1)
effect_unloading:          mmu_blue_anticlock_slow, (0, 0, 0.4)
effect_unloading_extruder: mmu_blue_anticlock_fast, (0, 0, 1)
effect_heating:            mmu_breathing_red,       (0.3, 0, 0)
effect_selecting:          mmu_white_fast,          (0.2, 0.2, 0.2)
effect_checking:           mmu_white_fast,          (0.8, 0.8, 0.8)
effect_initialized:        mmu_rainbow,             (0.5, 0.2, 0)
effect_error:              mmu_strobe,              (1, 0, 0)
effect_complete:           mmu_sparkle,             (0.3, 0.3, 0.3)
effect_gate_selected:      mmu_static_blue,         (0, 0, 1)
effect_gate_available:     mmu_static_white_dim,    (0.3, 0.3, 0.3)
effect_gate_available_sel: mmu_ready_white,         (0.75, 0.75, 0.75)
effect_gate_unknown:       mmu_static_orange,       (0.5, 0.2, 0)
effect_gate_unknown_sel:   mmu_ready_orange,        (0.75, 0.3, 0)
effect_gate_empty:         mmu_static_black,        (0, 0, 0)
effect_gate_empty_sel:     mmu_ready_red,           (0.2, 0, 0)
```

Add the below custom LED effect colors at the bottom of your **printer.cfg**. These are used in the LED effects above.

```
[mmu_led_effect mmu_static_white_dim]
define_on:    gates
layers:       static 0 0 top (0.3,0.3,0.3)

[mmu_led_effect mmu_ready_white]
define_on:    gates
layers:       breathing 2 0 subtract (0.4,0.4,0.4)
              static 0 0 top (0.5,0.5,0.5)

[mmu_led_effect mmu_ready_red]
define_on:    gates
layers:       breathing 2 0 subtract (0.4,0.0,0.0)
              static 0 0 top (0.5,0.0,0.0)
```

### Update mmu/addons/mmu_eject_buttons_hw.cfg
**Step 1: Clear the mmu_eject_buttons_hw.cfg file.** <br/><br/>
Start by completely deleting the content of that file and hitting save.

**Step 2: Paste the below configuration in the mmu_eject_buttons_hw.cfg file**<br/><br/>
The below starter setup is for an 8 lane unit. To set up a lower lane count, paste the complete content below and delete the corresponding [gcode_button mmu_eject_button_N] sections. If you have more than 8 lanes, add more blocks following the patterns below.
```
[gcode_button mmu_eject_button_0]
pin: mmu0:EJECT_BUTTON_0
press_gcode: _MMU_EJECT_BUTTON GATE=0

[gcode_button mmu_eject_button_1]
pin: mmu1:EJECT_BUTTON_1
press_gcode: _MMU_EJECT_BUTTON GATE=1

[gcode_button mmu_eject_button_2]
pin: mmu2:EJECT_BUTTON_2
press_gcode: _MMU_EJECT_BUTTON GATE=2

[gcode_button mmu_eject_button_3]
pin: mmu3:EJECT_BUTTON_3
press_gcode: _MMU_EJECT_BUTTON GATE=3

[gcode_button mmu_eject_button_4]
pin: mmu4:EJECT_BUTTON_4
press_gcode: _MMU_EJECT_BUTTON GATE=4

[gcode_button mmu_eject_button_5]
pin: mmu5:EJECT_BUTTON_5
press_gcode: _MMU_EJECT_BUTTON GATE=5

[gcode_button mmu_eject_button_6]
pin: mmu6:EJECT_BUTTON_6
press_gcode: _MMU_EJECT_BUTTON GATE=6

[gcode_button mmu_eject_button_7]
pin: mmu7:EJECT_BUTTON_7
press_gcode: _MMU_EJECT_BUTTON GATE=7
```

### Update printer.cfg
We will be updating the printer.cfg to add support for the BME humidity sensors as below. Similarly to the other files, remove or add the temperature sensor blocks to match your lane count.

```
[temperature_sensor Lane_0]
sensor_type: BME280
i2c_address: 118
i2c_mcu: mmu0
i2c_software_scl_pin: mmu0:PB3
i2c_software_sda_pin: mmu0:PB4

[temperature_sensor Lane_1]
sensor_type: BME280
i2c_address: 118
i2c_mcu: mmu1
i2c_software_scl_pin: mmu1:PB3
i2c_software_sda_pin: mmu1:PB4

[temperature_sensor Lane_2]
sensor_type: BME280
i2c_address: 118
i2c_mcu: mmu2
i2c_software_scl_pin: mmu2:PB3
i2c_software_sda_pin: mmu2:PB4

[temperature_sensor Lane_3]
sensor_type: BME280
i2c_address: 118
i2c_mcu: mmu3
i2c_software_scl_pin: mmu3:PB3
i2c_software_sda_pin: mmu3:PB4

[temperature_sensor Lane_4]
sensor_type: BME280
bme280_report_time: 20
i2c_address: 118
i2c_mcu: mmu4
i2c_software_scl_pin: mmu4:PB3
i2c_software_sda_pin: mmu4:PB4

[temperature_sensor Lane_5]
sensor_type: BME280
i2c_address: 118
i2c_mcu: mmu5
i2c_software_scl_pin: mmu5:PB3
i2c_software_sda_pin: mmu5:PB4

[temperature_sensor Lane_6]
sensor_type: BME280
bme280_report_time: 20
i2c_address: 118
i2c_mcu: mmu6
i2c_software_scl_pin: mmu6:PB3
i2c_software_sda_pin: mmu6:PB4

[temperature_sensor Lane_7]
sensor_type: BME280
i2c_address: 118
i2c_mcu: mmu7
i2c_software_scl_pin: mmu7:PB3
i2c_software_sda_pin: mmu7:PB4
```

### Save, restart and confirm lanes are visible
Once all of the above steps are completed hit save and restart klipper. The MMU hardware should now all be set up and all your lanes visible in the machine panel as below:

<p align="center">
  Installer screen
</p>

## Configuring Happy Hare
Now that the hardware is set up and visible to klipper, the next step is to configure the Happy Hare software to match the EMU capabilities and general Type B MMU good practice. That configuration will be predominately done in the mmu/base/mmu_parameters.cfg file. The indicated configuration below is geared towards reliability of feeding vs. filament swap speed. Use that as a starting point and tune to your liking once the unit is fully configured and operational.

### Setting up the EMU software parameters in mmu/base/mmu_parameters.cfg
Unlike the hardware setup files, do not delete the content of this file. We will be making targeted changes to match the EMU capabilities as validated through our testing.

**MMU Hardware Limits:** The EMU can operate up to a maximum of 500mm/sec feeding velocity and 400mm/sec2 acceleration. Adjust the maximum hardware limits as below.</br>
```
gear_max_velocity: 500
gear_max_accel: 400
```
**Logging:** Reduce log verbosity to reduce SD Card wear and system load</br></br>
```
log_level: 1
log_file_level: 1		
log_statistics: 0 		
log_visual: 1			
log_startup_status: 1		
log_m117_messages: 1
```			
**Speeds:** Our objective is reliability with operation. While the EMU can operate at 500mm/sec feeding, any snag in the filament path risks the lane stepper skipping steps. As such, it is recommended that conservative values are used in the speed set up, and tune up from there.</br>
```
gear_from_spool_speed: 250
gear_from_spool_accel: 120
#gear_from_buffer_speed: 250 # This is not necessary. Delete this line as there is no buffer.
#gear_from_buffer_accel: 120 # This is not necessary. Delete this line as there is no buffer.
gear_unload_speed: 250
gear_unload_accel: 120

gear_short_move_speed: 100
gear_short_move_accel: 100
gear_short_move_threshold: 100
gear_homing_speed: 100

extruder_load_speed: 16
extruder_unload_speed: 20
extruder_sync_load_speed: 16
extruder_sync_unload_speed: 20
extruder_homing_speed: 16

macro_toolhead_max_accel: 0
macro_toolhead_min_cruise_ratio: 0.5
```
**Gate load:** The EMU uses the post stepper (gear) switch sensor as the filament homing point for the lanes. That means that when swapping colors, the filament will retract all the way into the EMU dry box. This has three benefits which maximise flexibility in lane / base unit arrangements and reliability in feeding filament:
1. The filament is kept as dry as possible as it is now fully in the dry box. This results in lower probability of the filament snapping in the lane stepper gear due to it absorbing humidity from the environment.
2. There is no need for a sensor at the combiner, simplifying wiring setup and configuration.
3. You can expand to as many lanes as you want with any combination of passive combiners to bring the lane bowden tubes together to one that feeds the toolhead.

The downside is that the full bowden length needs to be traversed when loading, resulting in slightly longer loading times (however that is almost insignificant) and that the bowden length for each lane needs to be calibrated before first use (this is an automated process described later in this guide).

In addition, conservative homing max and preload homing max value have been selected, to allow the user time to load the filament and ensure it is gripped by the EMU lane stepper. 

It is therefore recommended to use the below values as is and do not modify unless trying to troubleshoot a specific issue.</br>
```
gate_homing_endstop: mmu_gear	
gate_homing_max: 600
gate_preload_homing_max: 600
gate_preload_parking_distance: 2
gate_unload_buffer: 50
gate_parking_distance: 2          # park the filament 2mm before the stepper exit switch. Do not increase this value beyond this as you are then risking the filament walking past the stepper gears.
gate_autoload: 1
gate_final_eject_distance: 100
```
**Bowden load:** As the EMU can accomodate long bowden tubes feeding to the printer, the bowden_homing_max is increased to allow Happy Hare to feed a longer run. 

In addition the correction and unload test moves are disabled as the encoder is not fitted in the base setup. From experience, encoders tend to accumulate dust after a few thousand swap cycles requiring ongoing maintenance. In addition they materially elevate the noise profile of the unit and add a point of "filament impact" in the bowden loading path.</br>
```
bowden_homing_max: 3000	# if the EMU lane to toolhead distance is larger than 3 meters, increase this value.

bowden_apply_correction: 0	
bowden_allowable_load_delta: 10.0

bowden_pre_unload_test: 0	
bowden_pre_unload_error_tolerance: 60 
```
**Extruder homing:** The below values are tuned to improve overall feeding reliability. The extruder homing max value has been increased, allowing for slight slippage during the bowden load to be compensated for. In addition, the homing buffer has been increased reducing the fast load speed 50mm before the filament arrives at the toolhead, to reduce possibility of filament impacting the gears.</br>
```
extruder_homing_max: 400			# Larger than the default HH value. This allows for homing to complete even if the filament skips steps during the load/
extruder_homing_endstop: extruder	
extruder_homing_buffer: 50
extruder_collision_homing_current: 100

extruder_force_homing: 0
```
**Toolhead Load:** This section needs to be populated following toolhead dimension calibration. Starter values from the community are available here: https://link.3dcoded.xyz/tipconfigs/ . 

In addition, the below settings have been adjusted to allow more tolerance in case of the extruder delaying grabbing the filament, which improves feeding reliability and allows for more "flex" in a slightly miss-tuned setup</br>
```
toolhead_homing_max: 250			# Increased from default of 40, to allow more tolerance in the extruder not grabbing the filament immediately.
toolhead_unload_safety_margin: 50	# Increased from the default of 10, to ensure filament is for sure clear of the extruder during unload.
toolhead_post_load_tighten: 0		# this is ignored as EMU is a Type B MMU - set to 0
toolhead_post_load_tension_adjust: 1	# Adjust tension post load to attemt to centre the sync feedback sensor. 
toolhead_entry_tension_test: 0		# Not required - toolhead sensor ensures feeding has happened.
```
**Tip Forming:** A toolhead cutter is highly recommended. Venture into tip forming at your own risk!</br>
```
force_form_tip_standalone: 1		  # Always standalone tip forming (TURN SLICER OFF!)
form_tip_macro: _MMU_CUT_TIP	
extruder_form_tip_current: 130		  # Bump up extruder current during tip forming. Helps ensure no skipped steps on the extruder if cutting is not 100% clean
slicer_tip_park_pos: 0			      # This specifies the position of filament in extruder after slicer completes tip forming. (TURN SLICER TIP FORMING OFF!)
```
**Purging:** If you have the blobifier set up, enable it here. For a baseline, starter setup, the below is recommended. Setting up the blobifier is recommended to be done after this guide is complete and your first test print is completed successfully.</br>
```
force_purge_standalone: 0 		# Use slicer purging (purge block) - set to 1 for blobifier
purge_macro: _MMU_PURGE			# Replace this with BLOBIFIER when set up
extruder_purge_current: 100		# leave this unchanged. If the extruder is skipping during purging with the blobifier you are most likely exceeding your hotend flow limit.
```
**Motor sync:** Setup sync feedback sensor (EMUSync) here. The sync multiplier high and low values allow for +/- 10% tolerance in rotation distance variation between your EMU lane and your extruder. If you find you need more than this for the unit to stay in sync then most likely either your extruder or EMU lane is not calibrated correctly.</br>
```
sync_gear_current: 80			    # 80% EMU stepper current during printing -> 0.64A
sync_feedback_enabled: 1		    # Enable EMU Sync sync feedback sensor
sync_feedback_buffer_range: 12		# EMU Sync switch to switch distance
sync_feedback_buffer_maxrange: 25	# EMU Sync max travel
sync_multiplier_high: 1.10		    # over-feed by 10% when in tension
sync_multiplier_low: 0.90		    # under-feed by 10% when in compression
```
**Filament Management:** Disable clog detection (as the encoder is not fitted to the unit) and enable endless spool (automated failover to the next available spool as defined in the gate map, administered via the Mainsail UI or Klipperscreen).</br>
```
enable_clog_detection: 0		
enable_endless_spool: 1			    # enable endless spool
endless_spool_on_load: 0	
endless_spool_eject_gate: -1		# Eject filament in the current gate
```
Here you can also configure spoolman filament management (highly recommended - instructions here:https://github.com/moggieuk/Happy-Hare/wiki/Spoolman-Support). </br></br>

**Calibration:** While happy hare can auto calibrate both the bowden tube length and lane rotation distance, I personally recommend a manual calibration for run to run consistency. Therefore all automated calibrations are disabled to ensure run-to-run consistency.</br>
```
autocal_bowden_length: 0	# Disable automated bowden length calibration
autotune_bowden_length: 0	# Disable automated bowden length tuning
skip_cal_rotation_distance: 0	# Require gate rotation distance calibration
autotune_rotation_distance: 0	# Disable automated gate calibration/tuning.
skip_cal_encoder: 0		# Encoder not fitted
autotune_encoder: 0		# Encoder not fitted
```

**Misc:** Minor options tuning and instructing Happy Hare that a filamentalist rewinder is used instead of a buffer </br>
```
timeout_pause: 86400		    # Idle time out in seconds. Set to 24 hours, to allow you to react and fix a pause if a swap issue materialises.
disable_heater: 60		        # Disable the hotend heater 60 seconds after an error is detected to reduce oozing.
default_extruder_temp: 230	    # Default temperature for performing swaps and forming tips when not in print (overridden by gate map). 230C is a good all around temperature for most material types.
extruder_temp_variance: 30	    # When waiting for extruder temperature this is the +/- permissible variance in degrees (>= 1).

startup_home_if_unloaded: 0	    # 0 = do nothing
startup_reset_ttg_map: 0	    #  0 = do nothing
show_error_dialog: 0		    # 0 = show error in console only. No mainsail pop-up
preload_attempts: 5		        # How many "grabbing" attempts are made to pick up the filament with preload feature
strict_filament_recovery: 0	    # If enabled with MMU with toolhead sensor, this will cause filament position recovery to
                                # perform extra moves to look for filament trapped in the space after extruder but before sensor
                                # This is largely uncessary but can be enabled if your toolhead setup is not particularly reliable.
filament_recovery_on_pause: 1	# Run a quick check to determine current filament position on pause/error.
retry_tool_change_on_error: 1	# Automatically retry a failed tool change. While this may mask a unit issue, we are aiming for relability during print.
bypass_autoload: 1		        # If extruder sensor fitted, this controls the automatic loading of extruder for bypass operation
has_filament_buffer: 0          # We are using a Filamentalist so no separate filament buffer is installed
#
# Advanced options. Don't mess unless you fully understand. Read documentation.
#
encoder_move_validation: 0	     # ADVANCED: 1 = Normally Encoder validates move distances are within given tolerance
                                 #           0 = Validation is disabled (eliminates slight pause between moves but less safe)
print_start_detection: 1	     # ADVANCED: Enabled for Happy Hare to automatically detect start and end of print and call
                                 # ADVANCED: MMU_PRINT_START and MMU_PRINT_END automatically. Harmless to leave enabled but can disable
                                 #           if you think it is causing problems and known START/END is covered in your macros
extruder: extruder		         # ADVANCED: Name of the toolhead extruder that MMU is using
gcode_load_sequence: 0		     # VERY ADVANCED: Gcode loading sequence 1=enabled, 0=internal logic (default)
gcode_unload_sequence: 0	     # VERY ADVANCED: Gcode unloading sequence, 1=enabled, 0=internal logic (default)
```

**Klipper:** Enable klipper timer too close (TTC) mitigations.</br>
```
update_trsync: 1		    # 1 = Increase TRSYNC_TIMEOUT, 0 = Leave the klipper default
canbus_comms_retries: 3		# Number of retries. Recommend the default of 3.
update_bit_max_time: 1		# 1 = Increase BIT_MAX_TIME, 0 = Leave the klipper default
update_aht10_commands: 0	# BTT ViViD specific setting. Leave at 0.
```

### Setting up the EMU software parameters in mmu/base/mmu_macro_vars.cfg
Unlike the hardware setup files, do not delete the content of this file. The below are some common settings that I have found usefull to change from default. However, the **detailed guide on Happy hare must be followed to set up your cut tip macro and to configure the system for your specific printer setup**. For more read here: https://github.com/moggieuk/Happy-Hare/wiki/Configuring-mmu_macro_vars.cfg

> [!WARNING]
> **WARNING: DO NOT RUN A PRINT WITHOUT CONFIGURING THE ABOVE.** The stock cut tip macro will most likely not work for your setup and you will crash the hotend on the cutter.

```
variable_min_toolchange_z       : 15.0 # Be safe and dont scratch the bed
variable_park_travel_speed      : 450  # Travel a bit faster to avoid stringing
```

## Calibrating the unit
Now that the baseline software is set up, the unit needs to be calibrated. There are 2 key calibrations that need to be done before the unit allows you to print.
1. Lane rotation distance
2. Bowden length per lane

Detailed instructions can be found here: https://github.com/moggieuk/Happy-Hare/wiki/MMU-Calibration-TypeB . The below will outline the mandatory minimum steps to calibrate the unit.

### Lane rotation distance calibration
Before you start with this calibration, remove all bowden tubes from the rear of the dry boxes going to the combiner. Add a short length of PTFE tubing (50mm is enough) to the first lane dry box exit. This will help guide the filament and not grind on the ecas connector. Then proceed to load some filament and execute the below instructions to grip it and feed it.

**Step 1:** Select the gate, load filament and move 200mm (or more) till the filament is showing from the unit exit ECAS connector.
```
MMU_SELECT GATE=0
MMU_TEST_MOVE MOVE=200 # run this once or more till you get filament out from the dry box.
```
**Step 2:** Cut the end of the filament poking out from the short ptfe tube attached to the dry box flush with the ptfe tube. Run the below command:
```
MMU_TEST_MOVE MOVE=100
```
Cut the filament again flush with the ptfe tube attached to the dry box. Measure it. Now use the below command to calibrate the rotation distance of the box.
```
MMU_CALIBRATE_GEAR MEASURED=102.5 #102.5 is an example value and should correspond to the value measured.
```
**Step 3:** Repeat for all lanes
```
MMU_SELECT GATE=1 # then 2,3,4, etc etc.
MMU_TEST_MOVE MOVE=200 # run this once or more till you get filament out from the dry box.
..... cut the filament at the box ptfe tube exit .....
MMU_TEST_MOVE MOVE=100
MMU_CALIBRATE_GEAR MEASURED=102.5 #102.5 is an example value and should correspond to the value measured.
```

> [!IMPORTANT]
> If you observe significant variation between gates, double check that your BMG gears are centred with the filament path and that the tension is approximately as equal as possible between them.

Rotation distance calibration is now done! 

### Bowden tube calibration
Now remove the short PTFE tube from the rear of the dry box and connect the combiner and your bowden tube to the EMU Sync and from there to the toolhead. The final calibration is to measure the length of bowden tube from the lane filament parking location to the toolhead. These will be different for each lane, hence these need to be individually calibrated following the procedure below.

> [!IMPORTANT]
> **IMPORTANT:** When calibrating bowden length for each lane, it is mandatory to keep the EMUSync manually held in the tension position, ie the two tubes brought towards each other. Why? The bowden calibration measures how much filament the lane feeds till the toolhead entry sensor is triggered. If the EMU Sync is left free, the springs can unpredictably compress/expand resulting in incorrect calibration. In addition, holding the EMU Sync in tension means the bowden length is slightly shorter. This helps avoid scenarios where the filament hits against the extruder if the lane rotation distance is slightly off.

```
MMU_SELECT GATE=0
MMU_CALIBRATE_BOWDEN
```
Repeat this for each lane, for example:
```
MMU_SELECT GATE=1 # then 2,3,4, etc etc.
MMU_CALIBRATE_BOWDEN
```
The unit calibration is now done and the unit is ready to be used!

## First start up
Follow the below first start up procedure to validate correct wiring of the EMU.

1. Load filament to each gate. The filament should be parked right before the post stepper sensor. In the UI, verify that the MMU Pre Gate sensor for the lane is marked as **detected** and the MMU Gear sensor for the lane is marked as **empty**. If not, you have them wired backwards. Swap their position in the mmu_hardware.cfg file.
2. Run the MMU_TEST_MOVE MOVE=50 command. Verify that the MMU Gear sensor for the lane is marked as **detected**. If not, you may have a wire break in the system.
3. Press the eject button. The filament should now be ejected from the unit. If not, you may have a wire break in the system.
4. Verify that the LEDs change color as the filament is inserted. From off to white for the eject button and off to white (if not using spoolman) for the led inside the box. If not, you may have either a power issue to the LED's or the in-out wiring sequence in the LED chain is wrong.
5. Validate your sync feedback sensor wiring. Bring the two sides of the bowden tube together. The tension switch should be showing as **detected** in the UI. Move the two sides of the bowden tube away from each other till the switch clicks. The compression switch should be showing as **detected** in the UI. If not, you have them wired backwards. Swap their position in the mmu_hardware.cfg file.
6. Home the printer, load filament to the first lane and type T0. The hotend should heat up to 230C and load filament to the toolhead. If the filament crashes to the extruder entry, your bowden distance calibration is off. If there is excessive material coming out of the nozzle, the toolhead calibration is off.

**After you have setup your Cut Tip macro** parameters:
1. Type MMU_UNLOAD. The toolhead should cut the filament and rewind to the EMU.
2. If the toolhead fails to cut, the cut tip macro is not configured correctly

## Next Steps
Finally you have to set up your slicer to recognise and operate with a multi-material unit. More instructions can be found here: https://github.com/moggieuk/Happy-Hare/wiki/Slicer-Setup

Optionally you can also set up:
1. Klipper screen integration: https://github.com/moggieuk/Happy-Hare/wiki/KlipperScreen
2. Mainsail / Fluid MMU panel: https://github.com/moggieuk/Happy-Hare/wiki/Mainsail-Fluidd-Integration
3. Spoolman: https://github.com/moggieuk/Happy-Hare/wiki/Spoolman-Support

## Seeking help

The Happy Hare discord is a great resource to help you going. Both in the general channel as well as the dedicated EMU channel. Link to the discord can be found here: https://discord.gg/aABQUjkZPk

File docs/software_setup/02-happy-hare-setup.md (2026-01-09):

# Happy Hare Setup Guide

This is a provisional sofware setup guide for the EMU using Happy Hare v3. This guide is meant to be read in conjunction with the Happy Hare setup guide as found here: https://github.com/moggieuk/Happy-Hare/wiki

## Table of Contents

- [Installing Happy Hare](#installing-happy-hare)
- [Configuring the EMU hardware](#configuring-the-emu-hardware)
- [Configuring Happy Hare parameters](#configuring-happy-hare-parameters)

## Installing Happy Hare
Install Happy Hare. More detailed instructions can be found here: https://github.com/moggieuk/Happy-Hare/wiki/Installation
```
cd ~
git clone https://github.com/moggieuk/Happy-Hare.git
cd ~/Happy-Hare
./install.sh -i
```
**Select MMU:** Pick option 16 - Other/Custom. <br/><br/>
<p align="center">
  Installer screen: Pick option 16 - Other/Custom
</p>

**Select MMU type:** Pick option 8 - Type-B (multiple filament drive steppers) with individual post-gear sensors, No Encoder <br/><br/>
<p align="center">
  Installer screen: Pick option 7 - Type-B with individual post-gear sensors, no encoder
</p>

**Select lane number:** Type the number of lanes you have set up. In my example below it is 8. <br/><br/>
<p align="center">
  Enter number of lanes (example: 8)
</p>

**Select the board used:** Pick option 15 - Not in list / Unknown <br/><br/>
<p align="center">
  Select board: option 15 Not in list / Unknown
</p>

**LED Support:** Enable LED support <br/><br/>
<p align="center">
  Enable LED support
</p>

**Endless Spool Support:** Enable Endless Spool support <br/><br/>
<p align="center">
  Enable Endless Spool support
</p>

**Include all the MMU config files:** Include all mmu config files in the printer.cfg <br/><br/>
<p align="center">
  Include MMU config files in printer.cfg
</p>

**(Optional) Mini 12864 screen support:** If you have a Mini 12864 screen, enabe the Happy Hare screen menu <br/><br/>
<p align="center">
  Enable Happy Hare menu for Mini 12864 (optional)
</p>

**Default pause/resume macros:** Include the default pause/resume macros from Happy Hare. Once the installation is complete, make sure you disable/remove any custom pause/resume macros that you may have in your existing Klipper installation! <br/><br/>
<p align="center">
  Include default pause/resume macros from Happy Hare
</p>

**EREC support:** Decline the installation of the EREC filament cutter <br/><br/>
<p align="center">
  Decline EREC filament cutter installation
</p>

**Moonraker.conf update:** Make sure your moonraker.conf contains [mmu_server] as below (should be inserted by HappyHare setup):
```
[file_manager]
enable_object_processing: True

[mmu_server]
enable_file_preprocessor: True
enable_toolchange_next_pos: True
update_spoolman_location: True
```

<br/><br/>
Baseline setup is now complete!
<br/><br/>
## Configuring the EMU hardware

### Update mmu/base/mmu.cfg
The Happy hare installer generates a generic mmu.cfg file that needs re-writing for the EMU. 

**Step 1: Clear the mmu.cfg file.** <br/><br/>
Start by completely deleting the content of that file and hitting save.

**Step 2: Update mmu.cfg with the EMU mcu boards definitions** <br/><br/>
For each lane you will need one distinct mcu mmu block defining the board name and the canbus UUID as noted earlier. In the example below I am using an 8 lane configuration. For a two lane setup, for example, you'd use `[mcu mmu0]` and `[mcu mmu1]` only.
```
[mcu mmu0]
canbus_uuid: your uuid 
canbus_interface: can0 # if you have multiple canbus buses, define here which canbus has the EMU units on it.

[mcu mmu1]
canbus_uuid: your uuid  
canbus_interface: can0

[mcu mmu2]
canbus_uuid: your uuid  
canbus_interface: can0

[mcu mmu3]
canbus_uuid: your uuid  
canbus_interface: can0

[mcu mmu4]
canbus_uuid: your uuid 
canbus_interface: can0

[mcu mmu5]
canbus_uuid: your uuid 
canbus_interface: can0

[mcu mmu6]
canbus_uuid: your uuid 
canbus_interface: can0

[mcu mmu7]
canbus_uuid: your uuid  
canbus_interface: can0
```

**Step 3: Update mmu.cfg with the EMU mcu board pin aliases** <br/><br/>
After the board definitions, insert the board pin aliases. 

> [!IMPORTANT]
> **Important note:** The first board defines the aliases for the tension and compression sensor too, so it is different to the rest. In the example below I am using an 8 lane configuration. Remove the corresponding `mmuN` reference from the mcu line to match the number of lanes you have (eg. `mcu: mmu0, mmu1` for a two lane setup).
```
[board_pins mmu]
mcu: mmu0, mmu1, mmu2, mmu3, mmu4, mmu5, mmu6, mmu7
aliases:
    MMU_GEAR_UART=PA15,
    MMU_GEAR_STEP=PD0,
    MMU_GEAR_DIR=PD1,
    MMU_GEAR_ENABLE=PD2,
    MMU_GEAR_DIAG=,

    MMU_NEOPIXEL=PD3,
    MMU_NEOPIXEL_LOGO=,

    MMU_PRE_GATE=PB7,
    MMU_POST_GEAR=PB5,

    MMU_TENSION=PB8,
    MMU_COMPRESSION=PB9,

    MMU_FAN=PA0,

    EJECT_BUTTON=PB6,
```
This file is now complete! 

### Update mmu/base/mmu_hardware.cfg

**Step 1: Clear the mmu_hardware.cfg file.** <br/><br/>
Start by completely deleting the content of that file and hitting save.

**Step 2: Paste the below configuration in the mmu_hardware.cfg file**<br/><br/>
The below starter setup is for an 8 lane unit. To set up a lower lane count, paste the complete content below and change the below:
1. **num_gates: 8 -> to equal to the number of lanes you have**
2. **Delete the unecessary tmc and stepper blocks**. For example if you have a 5 lane unit, delete `[tmc2209 stepper_mmu_gear_5]`, `[tmc2209 stepper_mmu_gear_6]`, `[tmc2209 stepper_mmu_gear_7]` blocks from the below.
3. **Delete the uncesessary pre_gate_switch_pin lines and post_gear_switch_pin lines**. For example for a 5 lane setup, remove `pre_gate_switch_pin_5`, `pre_gate_switch_pin_6`, `pre_gate_switch_pin_7`, `post_gear_switch_pin_5`, `post_gear_switch_pin_6`, `post_gear_switch_pin_7`
4. **Update the LED chain_count**: 16 is for 8 lanes. This needs to be equal to number of lanes x 2. So for a 5 lane setup this would be set to 10.
5. **Update the LED effect exit leds**: `exit_leds: neopixel:mmu_leds (1,3,5,7,9,11,13,15)` is for 8 lanes. For 5, this should be exit_leds: neopixel:mmu_leds (1,3,5,7,9)` .
6. **Update the LED effect entry leds**: `entry_leds: neopixel:mmu_leds (2,4,6,8,10,12,14,16)` is for 8 lanes. For 5, this should be `entry_leds: neopixel:mmu_leds (2,4,6,8,10)`

If you have more than 8 lanes, insert accordingly additional blocks, following the patterns as illustrated in the full configuration file below.

> [!TIP]
> If during testing you see that the EMU stepper spins backwards, invert the dir_pin by adding a ! infront of it (!dir_pin).

Finally, update your toolhead sensors definition to match your setup. Here I have the extruder entry (top) sensor in my toolhead can board named EBBCan connected to pin PB6 and the toolhead sensor (post extruder) at pin PB5.
```
extruder_switch_pin: ^EBBCan: PB6
toolhead_switch_pin: ^EBBCan: PB5
```

File contents - mmu_hardware.cfg:

```
[mmu_machine]
num_gates: 8			
mmu_vendor: Other			
mmu_version: 1.0			

selector_type: VirtualSelector
variable_bowden_lengths: 1		
variable_rotation_distances: 1		
require_bowden_move: 1		
filament_always_gripped: 1	
has_bypass: 1 

# FILAMENT DRIVE GEAR STEPPER  -----------------------------------------------------------------------------------------
[tmc2209 stepper_mmu_gear]
uart_pin: mmu0:MMU_GEAR_UART
run_current: 0.8		
hold_current: 0.2	
interpolate: False
sense_resistor: 0.110	
stealthchop_threshold: 1		

[stepper_mmu_gear]
step_pin: mmu0:MMU_GEAR_STEP
dir_pin: mmu0:MMU_GEAR_DIR
enable_pin: !mmu0:MMU_GEAR_ENABLE
rotation_distance: 22.7574		
gear_ratio: 1:1			
microsteps: 32				
full_steps_per_rotation: 200		

# Filament Drive Gear_1 --------------------------
[tmc2209 stepper_mmu_gear_1]
uart_pin: mmu1:MMU_GEAR_UART

[stepper_mmu_gear_1]
step_pin: mmu1:MMU_GEAR_STEP
dir_pin: mmu1:MMU_GEAR_DIR
enable_pin: !mmu1:MMU_GEAR_ENABLE

# Filament Drive Gear_2 --------------------------
[tmc2209 stepper_mmu_gear_2]
uart_pin: mmu2:MMU_GEAR_UART

[stepper_mmu_gear_2]
step_pin: mmu2:MMU_GEAR_STEP
dir_pin: mmu2:MMU_GEAR_DIR
enable_pin: !mmu2:MMU_GEAR_ENABLE

# Filament Drive Gear_3 --------------------------
[tmc2209 stepper_mmu_gear_3]
uart_pin: mmu3:MMU_GEAR_UART

[stepper_mmu_gear_3]
step_pin: mmu3:MMU_GEAR_STEP
dir_pin: mmu3:MMU_GEAR_DIR
enable_pin: !mmu3:MMU_GEAR_ENABLE

# Filament Drive Gear_4 --------------------------
[tmc2209 stepper_mmu_gear_4]
uart_pin: mmu4:MMU_GEAR_UART

[stepper_mmu_gear_4]
step_pin: mmu4:MMU_GEAR_STEP
dir_pin: mmu4:MMU_GEAR_DIR
enable_pin: !mmu4:MMU_GEAR_ENABLE

# Filament Drive Gear_5 --------------------------
[tmc2209 stepper_mmu_gear_5]
uart_pin: mmu5:MMU_GEAR_UART

[stepper_mmu_gear_5]
step_pin: mmu5:MMU_GEAR_STEP
dir_pin: mmu5:MMU_GEAR_DIR
enable_pin: !mmu5:MMU_GEAR_ENABLE

# Filament Drive Gear_6 --------------------------
[tmc2209 stepper_mmu_gear_6]
uart_pin: mmu6:MMU_GEAR_UART

[stepper_mmu_gear_6]
step_pin: mmu6:MMU_GEAR_STEP
dir_pin: mmu6:MMU_GEAR_DIR
enable_pin: !mmu6:MMU_GEAR_ENABLE

# Filament Drive Gear_7 --------------------------
[tmc2209 stepper_mmu_gear_7]
uart_pin: mmu7:MMU_GEAR_UART

[stepper_mmu_gear_7]
step_pin: mmu7:MMU_GEAR_STEP
dir_pin: mmu7:MMU_GEAR_DIR
enable_pin: !mmu7:MMU_GEAR_ENABLE

[mmu_sensors]
pre_gate_switch_pin_0: ^mmu0:MMU_PRE_GATE
pre_gate_switch_pin_1: ^mmu1:MMU_PRE_GATE
pre_gate_switch_pin_2: ^mmu2:MMU_PRE_GATE
pre_gate_switch_pin_3: ^mmu3:MMU_PRE_GATE
pre_gate_switch_pin_4: ^mmu4:MMU_PRE_GATE
pre_gate_switch_pin_5: ^mmu5:MMU_PRE_GATE
pre_gate_switch_pin_6: ^mmu6:MMU_PRE_GATE
pre_gate_switch_pin_7: ^mmu7:MMU_PRE_GATE

post_gear_switch_pin_0: ^mmu0:MMU_POST_GEAR
post_gear_switch_pin_1: ^mmu1:MMU_POST_GEAR
post_gear_switch_pin_2: ^mmu2:MMU_POST_GEAR
post_gear_switch_pin_3: ^mmu3:MMU_POST_GEAR
post_gear_switch_pin_4: ^mmu4:MMU_POST_GEAR
post_gear_switch_pin_5: ^mmu5:MMU_POST_GEAR
post_gear_switch_pin_6: ^mmu6:MMU_POST_GEAR
post_gear_switch_pin_7: ^mmu7:MMU_POST_GEAR

extruder_switch_pin: ^EBBCan: PB6
toolhead_switch_pin: ^EBBCan: PB5

sync_feedback_tension_pin: ^mmu0:MMU_TENSION         # Compression is when you pull the bowden tubes (entry/exit) away from each other. Tension when you push the tubes together.
sync_feedback_compression_pin: ^mmu0:MMU_COMPRESSION

# MMU NEOPIXEL LED SUPPORT ------------------------------------------------------------------------------------

[neopixel mmu_leds]
pin: mmu0:MMU_NEOPIXEL
chain_count: 16			# Number lanes x2
color_order: GRBW		# Set based on your particular neopixel specification

# MMU LED EFFECT SEGMENTS ----------------------------------------------------------------------------------------------

[mmu_leds unit0]
exit_leds:   neopixel:mmu_leds (1,3,5,7,9,11,13,15) # First, third, fifth LED and so forth.
entry_leds: neopixel:mmu_leds (2,4,6,8,10,12,14,16) # Second, fourth, sixth LED and so forth.
logo_leds:    
frame_rate: 24

enabled: True                           # LEDs are enabled at startup
animation: True                         # Use led-animation-effects
exit_effect: gate_status                # gate_status in the eject buttons
entry_effect: filament_color            # filament_color in the dry box LED
status_effect: off                      # no status LED is on the unit
logo_effect: (0, 0, 0)                  # no Logo LED is on the unit
white_light: (1, 1, 1)                  # RGB color for static white light
black_light: (1, 1, 1)                  # RGB color used to represent "black" filament
empty_light: (0.0, 0.0, 0.0)            # Empty gate has eject button "off"

effect_loading:            mmu_blue_clockwise_slow, (0, 0, 0.4)
effect_loading_extruder:   mmu_blue_clockwise_fast, (0, 0, 1)
effect_unloading:          mmu_blue_anticlock_slow, (0, 0, 0.4)
effect_unloading_extruder: mmu_blue_anticlock_fast, (0, 0, 1)
effect_heating:            mmu_breathing_red,       (0.3, 0, 0)
effect_selecting:          mmu_white_fast,          (0.2, 0.2, 0.2)
effect_checking:           mmu_white_fast,          (0.8, 0.8, 0.8)
effect_initialized:        mmu_rainbow,             (0.5, 0.2, 0)
effect_error:              mmu_strobe,              (1, 0, 0)
effect_complete:           mmu_sparkle,             (0.3, 0.3, 0.3)
effect_gate_selected:      mmu_static_blue,         (0, 0, 1)
effect_gate_available:     mmu_static_white_dim,    (0.3, 0.3, 0.3)
effect_gate_available_sel: mmu_ready_white,         (0.75, 0.75, 0.75)
effect_gate_unknown:       mmu_static_orange,       (0.5, 0.2, 0)
effect_gate_unknown_sel:   mmu_ready_orange,        (0.75, 0.3, 0)
effect_gate_empty:         mmu_static_black,        (0, 0, 0)
effect_gate_empty_sel:     mmu_ready_red,           (0.2, 0, 0)
```

### Update mmu/addons/mmu_eject_buttons_hw.cfg
**Step 1: Clear the mmu_eject_buttons_hw.cfg file.** <br/><br/>
Start by completely deleting the content of that file and hitting save.

**Step 2: Paste the below configuration in the mmu_eject_buttons_hw.cfg file**<br/><br/>
The below starter setup is for an 8 lane unit. To set up a lower lane count, paste the complete content below and delete the corresponding [gcode_button mmu_eject_button_N] sections. If you have more than 8 lanes, add more blocks following the patterns below.
```
[gcode_button mmu_eject_button_0]
pin: mmu0:EJECT_BUTTON
press_gcode: _MMU_EJECT_BUTTON GATE=0

[gcode_button mmu_eject_button_1]
pin: mmu1:EJECT_BUTTON
press_gcode: _MMU_EJECT_BUTTON GATE=1

[gcode_button mmu_eject_button_2]
pin: mmu2:EJECT_BUTTON
press_gcode: _MMU_EJECT_BUTTON GATE=2

[gcode_button mmu_eject_button_3]
pin: mmu3:EJECT_BUTTON
press_gcode: _MMU_EJECT_BUTTON GATE=3

[gcode_button mmu_eject_button_4]
pin: mmu4:EJECT_BUTTON
press_gcode: _MMU_EJECT_BUTTON GATE=4

[gcode_button mmu_eject_button_5]
pin: mmu5:EJECT_BUTTON
press_gcode: _MMU_EJECT_BUTTON GATE=5

[gcode_button mmu_eject_button_6]
pin: mmu6:EJECT_BUTTON
press_gcode: _MMU_EJECT_BUTTON GATE=6

[gcode_button mmu_eject_button_7]
pin: mmu7:EJECT_BUTTON
press_gcode: _MMU_EJECT_BUTTON GATE=7
```

### Upload the emu_macros.cfg file and reference it in your printer.cfg
The linked file here contains a set of configurations and definitions that are required for EMU to function. In addition, it contains a fan auto control macro, to minimize noise and ensure adequate unit cooling. File: https://github.com/DW-Tas/EMU/tree/main/macros

Upload that file in your klipper environment and add the below line to include it in your printer.cfg file:
```[include emu_macros.cfg]```

That file contains the **BME temperature and humidity sensor definitions** as below. It is set up for an 8 lane unit, so if you have less lanes, delete the corresponding blocks from the file.
```
[temperature_sensor Lane_N]
sensor_type: BME280
i2c_address: 118
i2c_mcu: mmu0  # mmu0=First lane, mmu1=second lane etc.
i2c_software_scl_pin: mmu0:PB3
i2c_software_sda_pin: mmu0:PB4
```
It also contains the definition of the onboard EBB temperature sensors used to control the unit fans. Similarly, it is set up for an 8 lane unit, so if you have less lanes, delete the corresponding blocks from the file.
```
[temperature_sensor _Lane_N_onboard]
sensor_type: temperature_mcu
sensor_mcu: mmu0 # mmu0=First lane, mmu1=second lane etc.
min_temp: 0
max_temp: 130
```
In addition, it contains the fan definitions for the unit as below. Similarly, it is set up for an 8 lane unit, so if you have less lanes, delete the corresponding blocks from the file.
```
[fan_generic _emu_fan_N]
pin: mmu0:MMU_FAN # mmu0=First lane, mmu1=second lane etc.
max_power: 1
kick_start_time: 0.5
```
Finally it contains the fan control macro that controls the fans on a by-lane basis. In the variable_sensors add the names of the **_Lane_N_onboard temperature sensors**, separated by a comma. In the variable_fans add the names of the **base unit fans**, separated by a comma. 

> [!NOTE]
> Prefixing the fans and board temperature sensors with a _ will hide them from the Mainsail UI, which is helpful to reduce clutter once you have your setup tuned and validated.

> [!IMPORTANT]
> The length of these two lists must match and correspond to each other (ie lane 0 fan and lane 0 onboard temp sensor must be first on the list etc).
> Make sure you include the **onboard temperature sensors in the fan control macro, not the BME sensors!**

Finally you can set the temperature where the fans turn on and off. By default, they are set to turn on at 39C and turn off at 37C.

```[gcode_macro MMU_FAN_CFG]
description: Holds configuration/state for multi fan controller.
variable_on_temp: 39.0
variable_off_temp: 37.0
variable_poll_s: 5.0
variable_enabled: True
variable_forced: -1                 # -1=AUTO, 0=all OFF, 1=all ON (global)
variable_sensors: "_Lane_0_onboard,_Lane_1_onboard,_Lane_2_onboard,_Lane_3_onboard,_Lane_4_onboard,_Lane_5_onboard,_Lane_6_onboard,_Lane_7_onboard"   # Comma-separated temperature_sensor names
variable_fans:    "_emu_fan_0,_emu_fan_1,_emu_fan_2,_emu_fan_3,_emu_fan_4,_emu_fan_5,_emu_fan_6,_emu_fan_7"  # Comma-separated fan_generic names
variable_warned_len_mismatch: False # internal: warn once per enable
gcode:
```
That file also contains some bespoke LED effects for the EMU, which are used earlier in the LED setup section.

### Save, restart and confirm lanes are visible
Once all of the above steps are completed hit save and restart klipper. The MMU hardware should now all be set up and all your lanes visible in the machine panel as below:

<p align="center">
  Installer screen
</p>

## Configuring Happy Hare parameters
Now that the hardware is set up and visible to klipper, the next step is to configure the Happy Hare software to match the EMU capabilities and general Type B MMU good practice. That configuration will be predominately done in the mmu/base/mmu_parameters.cfg file. The indicated configuration below is geared towards reliability of feeding vs. filament swap speed. Use that as a starting point and tune to your liking once the unit is fully configured and operational.

### Setting up the EMU software parameters in mmu/base/mmu_parameters.cfg
Unlike the hardware setup files, do not delete the content of this file. We will be making targeted changes to match the EMU capabilities as validated through our testing.

**MMU Hardware Limits:** The EMU can operate up to a maximum of 500mm/sec feeding velocity and 400mm/sec2 acceleration. Adjust the maximum hardware limits as below.</br>
```
gear_max_velocity: 500
gear_max_accel: 400
```
**Logging:** Reduce log verbosity to reduce SD Card wear and system load</br></br>
```
log_level: 1
log_file_level: 1		
log_statistics: 0 		
log_visual: 1			
log_startup_status: 1		
log_m117_messages: 1
```			
**Speeds:** Our objective is reliability with operation. While the EMU can operate at 500mm/sec feeding, any snag in the filament path risks the lane stepper skipping steps. As such, it is recommended that conservative values are used in the speed set up, and tune up from there.</br>
```
gear_from_spool_speed: 250
gear_from_spool_accel: 120
#gear_from_buffer_speed: 250 # This is not necessary. Delete this line as there is no buffer.
#gear_from_buffer_accel: 120 # This is not necessary. Delete this line as there is no buffer.
gear_unload_speed: 250
gear_unload_accel: 120

gear_short_move_speed: 100
gear_short_move_accel: 100
gear_short_move_threshold: 100
gear_homing_speed: 100

extruder_load_speed: 16
extruder_unload_speed: 20
extruder_sync_load_speed: 16
extruder_sync_unload_speed: 20
extruder_homing_speed: 16

macro_toolhead_max_accel: 0
macro_toolhead_min_cruise_ratio: 0.5
```
**Gate load:** The EMU uses the post stepper (gear) switch sensor as the filament homing point for the lanes. That means that when swapping colors, the filament will retract all the way into the EMU dry box. This has three benefits which maximise flexibility in lane / base unit arrangements and reliability in feeding filament:
1. The filament is kept as dry as possible as it is now fully in the dry box. This results in lower probability of the filament snapping in the lane stepper gear due to it absorbing humidity from the environment.
2. There is no need for a sensor at the combiner, simplifying wiring setup and configuration.
3. You can expand to as many lanes as you want with any combination of passive combiners to bring the lane bowden tubes together to one that feeds the toolhead.

The downside is that the full bowden length needs to be traversed when loading, resulting in slightly longer loading times (however that is almost insignificant) and that the bowden length for each lane needs to be calibrated before first use (this is an automated process described later in this guide).

In addition, conservative homing max and preload homing max value have been selected, to allow the user time to load the filament and ensure it is gripped by the EMU lane stepper. 

It is therefore recommended to use the below values as is and do not modify unless trying to troubleshoot a specific issue.</br>
```
gate_homing_endstop: mmu_gear	
gate_homing_max: 600
gate_preload_homing_max: 600
gate_preload_parking_distance: 1
gate_unload_buffer: 100
gate_parking_distance: 1          # park the filament 1mm before the stepper exit switch. Do not increase this value beyond this as you are then risking the filament walking past the stepper gears.
gate_autoload: 1
gate_final_eject_distance: 100
```
**Bowden load:** As the EMU can accomodate long bowden tubes feeding to the printer, the bowden_homing_max is increased to allow Happy Hare to feed a longer run. 

In addition the correction and unload test moves are disabled as the encoder is not fitted in the base setup. From experience, encoders tend to accumulate dust after a few thousand swap cycles requiring ongoing maintenance. In addition they materially elevate the noise profile of the unit and add a point of "filament impact" in the bowden loading path.</br>
```
bowden_homing_max: 3000	# if the EMU lane to toolhead distance is larger than 3 meters, increase this value.

bowden_apply_correction: 0	
bowden_allowable_load_delta: 10.0

bowden_pre_unload_test: 0	
bowden_pre_unload_error_tolerance: 60 
```
**Extruder homing:** The below values are tuned to improve overall feeding reliability. The extruder homing max value has been increased, allowing for slight slippage during the bowden load to be compensated for. In addition, the homing buffer has been increased reducing the fast load speed 50mm before the filament arrives at the toolhead, to reduce possibility of filament impacting the gears.</br>
```
extruder_homing_max: 400			# Larger than the default HH value. This allows for homing to complete even if the filament skips steps during the load/
extruder_homing_endstop: extruder	
extruder_homing_buffer: 50
extruder_collision_homing_current: 100

extruder_force_homing: 0
```
**Toolhead Load:** This section needs to be populated following toolhead dimension calibration. Starter values from the community are available here: https://link.3dcoded.xyz/tipconfigs/ . 

In addition, the below settings have been adjusted to allow more tolerance in case of the extruder delaying grabbing the filament, which improves feeding reliability and allows for more "flex" in a slightly miss-tuned setup</br>
```
toolhead_homing_max: 250			# Increased from default of 40, to allow more tolerance in the extruder not grabbing the filament immediately.
toolhead_unload_safety_margin: 90	# Increased from the default of 10, to ensure filament is for sure clear of the extruder during unload.
toolhead_post_load_tighten: 0		# this is ignored as EMU is a Type B MMU - set to 0
toolhead_post_load_tension_adjust: 1	# Adjust tension post load to attemt to centre the sync feedback sensor. 
toolhead_entry_tension_test: 0		# Not required - toolhead sensor ensures feeding has happened.
```
**Tip Forming:** A toolhead cutter is highly recommended. Venture into tip forming at your own risk!</br>
```
force_form_tip_standalone: 1		  # Always standalone tip forming (TURN SLICER OFF!)
form_tip_macro: _MMU_CUT_TIP	
extruder_form_tip_current: 130		  # Bump up extruder current during tip forming. Helps ensure no skipped steps on the extruder if cutting is not 100% clean
slicer_tip_park_pos: 0			      # This specifies the position of filament in extruder after slicer completes tip forming. (TURN SLICER TIP FORMING OFF!)
```
**Purging:** If you have the blobifier set up, enable it here. For a baseline, starter setup, the below is recommended. Setting up the blobifier is recommended to be done after this guide is complete and your first test print is completed successfully.</br>
```
force_purge_standalone: 0 		# Use slicer purging (purge block) - set to 1 for blobifier
purge_macro: 			            # Replace this with BLOBIFIER when set up. Leave empty if not using the blobifier. 
extruder_purge_current: 100		# leave this unchanged. If the extruder is skipping during purging with the blobifier you are most likely exceeding your hotend flow limit.
```
**Motor sync:** Setup sync feedback sensor (EMUSync) here. The sync multiplier high and low values allow for +/- 10% tolerance in rotation distance variation between your EMU lane and your extruder. If you find you need more than this for the unit to stay in sync then most likely either your extruder or EMU lane is not calibrated correctly.</br>
```
sync_gear_current: 50			    # 50% EMU stepper current during printing -> ~0.4A when printing. Higher than 0.5A can cause PLA to clog the EMU stepper in hot environments.
sync_feedback_enabled: 1		    # Enable EMU Sync sync feedback sensor
sync_feedback_buffer_range: 12		# EMU Sync switch to switch distance
sync_feedback_buffer_maxrange: 25	# EMU Sync max travel
sync_multiplier_high: 1.10		    # over-feed by 10% when in tension
sync_multiplier_low: 0.90		    # under-feed by 10% when in compression
```
**Filament Management:** Disable clog detection (as the encoder is not fitted to the unit) and enable endless spool (automated failover to the next available spool as defined in the gate map, administered via the Mainsail UI or Klipperscreen).</br>
```
enable_clog_detection: 0		
enable_endless_spool: 1			    # enable endless spool
endless_spool_on_load: 0	
endless_spool_eject_gate: -1		# Eject filament in the current gate
```
Here you can also configure spoolman filament management (highly recommended - instructions here:https://github.com/moggieuk/Happy-Hare/wiki/Spoolman-Support). </br></br>

**Calibration:** While happy hare can auto calibrate both the bowden tube length and lane rotation distance, I personally recommend a manual calibration for run to run consistency. Therefore all automated calibrations are disabled to ensure run-to-run consistency.</br>
```
autocal_bowden_length: 0	# Disable automated bowden length calibration
autotune_bowden_length: 0	# Disable automated bowden length tuning
skip_cal_rotation_distance: 0	# Require gate rotation distance calibration
autotune_rotation_distance: 0	# Disable automated gate calibration/tuning.
skip_cal_encoder: 0		# Encoder not fitted
autotune_encoder: 0		# Encoder not fitted
```

**Misc:** Minor options tuning and instructing Happy Hare that a filamentalist rewinder is used instead of a buffer </br>
```
timeout_pause: 86400		    # Idle time out in seconds. Set to 24 hours, to allow you to react and fix a pause if a swap issue materialises.
disable_heater: 60		        # Disable the hotend heater 60 seconds after an error is detected to reduce oozing.
default_extruder_temp: 230	    # Default temperature for performing swaps and forming tips when not in print (overridden by gate map). 230C is a good all around temperature for most material types.
extruder_temp_variance: 30	    # When waiting for extruder temperature this is the +/- permissible variance in degrees (>= 1).

startup_home_if_unloaded: 0	    # 0 = do nothing
startup_reset_ttg_map: 0	    #  0 = do nothing
show_error_dialog: 0		    # 0 = show error in console only. No mainsail pop-up
preload_attempts: 5		        # How many "grabbing" attempts are made to pick up the filament with preload feature
strict_filament_recovery: 0	    # If enabled with MMU with toolhead sensor, this will cause filament position recovery to
                                # perform extra moves to look for filament trapped in the space after extruder but before sensor
                                # This is largely uncessary but can be enabled if your toolhead setup is not particularly reliable.
filament_recovery_on_pause: 1	# Run a quick check to determine current filament position on pause/error.
retry_tool_change_on_error: 1	# Automatically retry a failed tool change. While this may mask a unit issue, we are aiming for relability during print.
bypass_autoload: 1		        # If extruder sensor fitted, this controls the automatic loading of extruder for bypass operation
has_filament_buffer: 0          # We are using a Filamentalist so no separate filament buffer is installed
#
# Advanced options. Don't mess unless you fully understand. Read documentation.
#
encoder_move_validation: 0	     # ADVANCED: 1 = Normally Encoder validates move distances are within given tolerance
                                 #           0 = Validation is disabled (eliminates slight pause between moves but less safe)
print_start_detection: 1	     # ADVANCED: Enabled for Happy Hare to automatically detect start and end of print and call
                                 # ADVANCED: MMU_PRINT_START and MMU_PRINT_END automatically. Harmless to leave enabled but can disable
                                 #           if you think it is causing problems and known START/END is covered in your macros
extruder: extruder		         # ADVANCED: Name of the toolhead extruder that MMU is using
gcode_load_sequence: 0		     # VERY ADVANCED: Gcode loading sequence 1=enabled, 0=internal logic (default)
gcode_unload_sequence: 0	     # VERY ADVANCED: Gcode unloading sequence, 1=enabled, 0=internal logic (default)
```

**Klipper:** Enable klipper timer too close (TTC) mitigations.</br>
```
update_trsync: 1		    # 1 = Increase TRSYNC_TIMEOUT, 0 = Leave the klipper default
canbus_comms_retries: 3		# Number of retries. Recommend the default of 3.
update_bit_max_time: 1		# 1 = Increase BIT_MAX_TIME, 0 = Leave the klipper default
update_aht10_commands: 0	# BTT ViViD specific setting. Leave at 0.
```

### Setting up the EMU software parameters in mmu/base/mmu_macro_vars.cfg
Unlike the hardware setup files, do not delete the content of this file. The below are some common settings that I have found usefull to change from default. However, the **detailed guide on Happy hare must be followed to set up your cut tip macro and to configure the system for your specific printer setup**. For more read here: https://github.com/moggieuk/Happy-Hare/wiki/Configuring-mmu_macro_vars.cfg

> [!WARNING]
> **WARNING: DO NOT RUN A PRINT WITHOUT CONFIGURING THE ABOVE.** The stock cut tip macro will most likely not work for your setup and you will crash the hotend on the cutter.

```
variable_min_toolchange_z       : 15.0 # Be safe and dont scratch the bed
variable_park_travel_speed      : 450  # Travel a bit faster to avoid stringing
```

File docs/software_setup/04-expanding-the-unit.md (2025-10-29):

# EMU Happy Hare Hardware and Software Setup Guide

This is a provisional sofware setup guide for the EMU using Happy Hare v3. This guide is meant to be read in conjunction with the Happy Hare setup guide as found here: https://github.com/moggieuk/Happy-Hare/wiki

## Table of Contents

- [Expanding the unit with more lanes](#expanding-the-unit-with-more-lanes)

## Expanding the unit with more lanes
Beyond the electrical connections, the below steps need to be undertaken when adding additional lanes to the EMU unit.

**mmu.cfg**

Add an additional MCU block for each new lane:
```
[mcu mmuN]
canbus_uuid: UUID 
canbus_interface: can0
```

Add an additional boards pin block:
```
[board_pins mmuN]
mcu: mmuN
aliases:

    MMU_GEAR_UART_N=PA15,
    MMU_GEAR_STEP_N=PD0,
    MMU_GEAR_DIR_N=PD1,
    MMU_GEAR_ENABLE_N=PD2,
    MMU_GEAR_DIAG_N=,

    MMU_PRE_GATE_N=PB7,
    MMU_POST_GEAR_N=PB5,

    EJECT_BUTTON_N=PB6,
```

**mmu_hardware.cfg:**

Update the below to reflect your current lane count:
```
[mmu_machine]
num_gates: 8
```
Add additional stepper definitions, where N is the lane number:
```
...
[tmc2209 stepper_mmu_gear_N]
uart_pin: mmuN:MMU_GEAR_UART_N

[stepper_mmu_gear_N]
step_pin: mmuN:MMU_GEAR_STEP_N
dir_pin: mmuN:MMU_GEAR_DIR_N
enable_pin: !mmuN:MMU_GEAR_ENABLE_N
...
```

Define the additional pre-gate and post gear sensors (pre-stepper, post-stepper)
```
[mmu_sensors]
...
pre_gate_switch_pin_N: ^mmuN:MMU_PRE_GATE_N
post_gear_switch_pin_N: ^mmuN:MMU_POST_GEAR_N
...
```

Increase your neopixel chain count to match the total number of lanes multipled by 2
```
[neopixel mmu_leds]
chain_count: NN			# Number lanes x2
```

Update the mmu_led's entry and exit LED numbers
```
[mmu_leds unit0]
exit_leds:   neopixel:mmu_leds (1,3,5,7,9,11,13,15, NN)
entry_leds: neopixel:mmu_leds (2,4,6,8,10,12,14,16, NN)
```

**mmu_eject_buttons_hw.cfg**

Define the additional eject buttons in the mmu_eject_buttons_hw.cfg file:
```
[gcode_button mmu_eject_button_N]
pin: mmuN:EJECT_BUTTON_N
press_gcode: _MMU_EJECT_BUTTON GATE=N
```

**mmu_macro_vars.cfg:**

Add an additional tool change gcode macro at the end of the file for each new lane:
```
[gcode_macro TN]
gcode: MMU_CHANGE_TOOL TOOL=N
```

**emu_macros.cfg**

Add additional temperature sensor, fan and BME sensor definitions and update the custom fan control macro to use them

Finally dont forget to execute the 2 calibrations for the new lanes - MMU_CALIBRATE_BOWDEN and  MMU_CALIBRATE_GEAR as descibed in the calibration section.

```
[temperature_sensor Lane_N]
sensor_type: BME280
i2c_address: 118
i2c_mcu: mmuN
i2c_software_scl_pin: mmuN:PB3
i2c_software_sda_pin: mmuN:PB4

[temperature_sensor Lane_N_onboard]
sensor_type: temperature_mcu
sensor_mcu: mmuN
min_temp: 0
max_temp: 130

[fan_generic emu_fan_N]
pin: mmuN:PA0
max_power: 1
kick_start_time: 0.5

[gcode_macro MMU_FAN_CFG]
...
variable_sensors: ".....,Lane_N_onboard"
variable_fans:    "......,emu_fan_N"
...
```

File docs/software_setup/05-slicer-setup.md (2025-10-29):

# Slicer setup and optimisation for multi color prints

Orca slicer is the recommended slicer for the EMU. The guide below will take you through a set of mandatory and recommended settings to help you achieve the best results possible from your EMU. The guide assumes that you are using a toolhead equipped with a cutter. Therefore all tip forming activity in the slicer will be disabled.

<p align="center">
  1 (4)
  1 (5)
  1 (2)
  1 (3)
</p>

## Table of Contents

- [Orca slicer mandatory setup](#orca-slicer-mandatory-setup)
  - [Machine G-Code setup](#machine-g-code-setup)
    - [Machine Start G-code](#machine-start-g-code)
    - [Machine End G-code](#machine-end-g-code)
    - [Layer change G-code](#layer-change-g-code)
    - [Change Filament G-code](#change-filament-g-code)
  - [Multi Material setup](#multi-material-setup)
  - [Extruder setup](#extruder-setup)
  - [Filament selection](#filament-selection)
- [Orca slicer profile tuning for multi-color printing](#orca-slicer-profile-tuning-for-multi-color-printing)
  - [Reducing color bleed](#reducing-color-bleed)
    - [Maximise the time spent printing hidden features before moving to the outer wall](#maximise-the-time-spent-printing-hidden-features-before-moving-to-the-outer-wall)
    - [Disable flush into objects' infill and support](#disable-flush-into-objects-infill-and-support)
    - [Use 3 (or more) walls](#use-3-or-more-walls)
    - [Use the blobifier](#use-the-blobifier)
    - [Tune your purge multiplier](#tune-your-purge-multiplier)
    - [Increase your variable_retract_length (mmu_macro_vars.cfg)](#increase-your-variable_retract_length-mmu_macro_varscfg)
  - [Optimising Print Quality](#optimising-print-quality)
    - [Speed settings](#speed-settings)
    - [Quality settings](#quality-settings)

## Orca slicer mandatory setup

### Machine G-Code setup
#### Machine Start G-code:
The Orca Slicer print start gcode is required to be amended to include the below additions. 
```
MMU_START_SETUP INITIAL_TOOL={initial_tool} TOTAL_TOOLCHANGES=!total_toolchanges! REFERENCED_TOOLS=!referenced_tools! TOOL_COLORS=!colors! TOOL_TEMPS=!temperatures! TOOL_MATERIALS=!materials! FILAMENT_NAMES=!filament_names! PURGE_VOLUMES=!purge_volumes!
MMU_START_CHECK
PRINT_START HOTEND=[nozzle_temperature_initial_layer] BED=[bed_temperature_initial_layer_single] CHAMBER=[chamber_temperature]
MMU_START_LOAD_INITIAL_TOOL
SET_PRINT_STATS_INFO TOTAL_LAYER={total_layer_count} ; For pause at layer functionality and better print stats
```
> [!WARNING]
> Replace the print start line with your existing print start command!

#### Machine End G-code:
The Orca Slicer print end gcode is required to be amended to include the below additions. 
```
MMU_END
PRINT_END ; your existing print end macro
```
> [!WARNING]
> Replace the print end line with your existing print end command!

#### Layer change G-code
```
; ... your existing layer change G-code...
_MMU_UPDATE_HEIGHT
```

#### Change Filament G-code
If using a purge block set up:
```
T[next_extruder]
```
If you have the blobifier add-on set up, add the below change filament g-code. This will enable purge volume reporting in the slicer.
```
T[next_extruder]
; FLUSH_START
; EXTERNAL_PURGE {flush_length}
; FLUSH_END
```

### Multi Material setup
Ensure that in the Multi Material tab, the below settings are set up:
1. Single Extruder Multi Material = selected
2. Extruders = 1
3. Manual Filament Change = de-selected
4. Purge in prime tower = selected. Deselect only if using the blobifier or similar purging system
5. Enable filament ramming = de-selected
6. Single extruder multi-material parameters - all set to 0 and high extruder current on filament swap = de-selected
7. Set up the advanced section with the approximate filament swap times - you can get these by typing MMU_STATS in the printer console after you have successfully ran a few multi-color prints

**No blobifier:**
<p align="center">
  
</p>

**With the blobifier:**
<p align="center">
  
</p>

### Extruder setup
Ensure that in the Extruder tab, the below settings are set up:
1. Retraction when switching material = 0

<p align="center">
  
</p>

### Filament selection
Using the (+) button, add as many filaments as available lanes in your EMU. 

<p align="center">
  
</p>

## Orca slicer profile tuning for multi-color printing

### Reducing color bleed
One of the biggest downsides to multi-color printing with a single nozzle is **the potential for color bleed**. This is usually the case when:
1. When swapping from **high saturation colors (red, black) to white**
2. Combined with **too low of a purge volume**
3. And using a **long meltzone hotend**

This happens due to the **molten material sticking to the hotend melt zone** and requiring disproportional amount of filament to "disrupt" that boundary layer and flush the color through. This is made worse by the fact that **filament flows in a laminar way**, hence there is little to no "turbulance" in the hotend to disrupt that layer.. 

Ways to mitigate include:
1. Use a regular flow (not a CHT) nozzle. The extra filament channels multiply the surface area that the boundary layer can be created against
2. Use a small meltzone nozzle. For multi-color printing, the vast majority of print time is spent swapping filaments and purging. Hence a lower flow hotent will not impact overall print speed by a significant factor

In addition to the above physical changes, the **below slicer settings can help** contain the color bleed

#### Maximise the time spend printing hidden features before moving to the outer wall
1. Enable Inner Outer Inner wall ordering mode.
2. Enable print infill first.
Printing **infill first results in the printer spending more time printing inside the model** before transitioning to the visible surfaces of the model (outer wall). It, therefore, increases the amount of filament extruded before the outer walls are printed and the probability that the outer walls will not show color bleed. **Inner Outer Inner wall ordering hides the resulting artefacts** from printing infill first.

For comparison, outer inner wall ordering mode must be avoided as it will print the external facing walls first, immediately after a color change!

<p align="center">
  
</p>

#### Disable flush into objects' infill and support
Similarly to the point above, disabling these settings ensures that **your defined purge volume is spent outside the model**.

<p align="center">
  
</p>

#### Use 3 (or more) walls
As above, the more walls printed before the outer perimeter, the higher the chance that the external walls are printed without color bleed.

<p align="center">
  
</p>

#### Use the blobifier
The blobifier algorithm **executes purging with varying speeds**, which helps **disrupt the laminar flow** of the filament against the walls. If your printer can accomodate the blobifier setup, it is strongly recommended that you set it up.

<p align="center">
  
</p>

In the picture above, you can see the no color bleed transition between white and black on the same layer. In addition you can observe the "ripples" created on the purge blobs due to the blobifier varying the purge speed and retracting and de-retracting during the purge, to flush out the filament from the nozzle.

> [!NOTE]
> If you are using the blobifier **do not disable the prime tower**. The prime tower will not be used to "purge" filament, rather **re-prime the nozzle**, clear out any air bubbles in the hotend that may have occured during the purge process and equalize nozzle pressure before resuming printing on the model. <br/>
> Set the prime volume to be equal to your meltzone volume **(meltzone length in mm * 2.4)**

<p align="center">
  
</p>

#### Tune your purge multiplier
Reducing the purge multiplier to 0.8-0.7 will indeed save some purge material; however more likely than not (unless you are using a particularly small meltzone hotend) it will result in color bleed. Now depending on how clean you want your prints to look, a purge multiplier of 1.2-1.25 (or more) is not unusual.

<p align="center">
  
</p>

> [!NOTE]
> Make sure your **nozzle volume is accurately set in the slicer** settings!

<p align="center">
  
</p>

#### Increase your variable_retract_length (mmu_macro_vars.cfg)
Reducing the amount of left over filament in the hotend can help reduce slightly the amount of material needing to be purged. I**ncreasing the variable_retract_length value to be ~5-10mm less than the variable_blade_pos** is recommended. 

> [!IMPORTANT]
> Make sure you **enable variable_simple_tip_forming**. It reduces the probability of clogs at the hotend when performing large retractions!

### Optimising Print Quality
As the vast majority of the time during multi-color printing is spent in tool swapping, you can afford to set conservative print settings which can materially improve the produced output with very little time tradeoff.

The below are my preferred settings for multi-color printing.

**Speed settings:**
<p align="center">
  1 (4)
  1 (5)
</p>

**Quality settings:**
<p align="center">
  1 (4)
  1 (5)
  1 (5)
</p>

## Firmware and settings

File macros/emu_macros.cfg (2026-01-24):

# === EMU Lane Temperature and Humidity Sensors ===

[temperature_sensor Lane_0]
sensor_type: BME280
i2c_address: 118
i2c_mcu: mmu0
i2c_software_scl_pin: mmu0:PB3
i2c_software_sda_pin: mmu0:PB4

[temperature_sensor Lane_1]
sensor_type: BME280
i2c_address: 118
i2c_mcu: mmu1
i2c_software_scl_pin: mmu1:PB3
i2c_software_sda_pin: mmu1:PB4

[temperature_sensor Lane_2]
sensor_type: BME280
i2c_address: 118
i2c_mcu: mmu2
i2c_software_scl_pin: mmu2:PB3
i2c_software_sda_pin: mmu2:PB4

[temperature_sensor Lane_3]
sensor_type: BME280
i2c_address: 118
i2c_mcu: mmu3
i2c_software_scl_pin: mmu3:PB3
i2c_software_sda_pin: mmu3:PB4

[temperature_sensor Lane_4]
sensor_type: BME280
i2c_address: 118
i2c_mcu: mmu4
i2c_software_scl_pin: mmu4:PB3
i2c_software_sda_pin: mmu4:PB4

[temperature_sensor Lane_5]
sensor_type: BME280
i2c_address: 118
i2c_mcu: mmu5
i2c_software_scl_pin: mmu5:PB3
i2c_software_sda_pin: mmu5:PB4

[temperature_sensor Lane_6]
sensor_type: BME280
i2c_address: 118
i2c_mcu: mmu6
i2c_software_scl_pin: mmu6:PB3
i2c_software_sda_pin: mmu6:PB4

[temperature_sensor Lane_7]
sensor_type: BME280
i2c_address: 118
i2c_mcu: mmu7
i2c_software_scl_pin: mmu7:PB3
i2c_software_sda_pin: mmu7:PB4


# === MMU Fan Auto-Control Configuration ===

# === Temperature sensors ===
[temperature_sensor _Lane_0_onboard]
sensor_type: temperature_mcu
sensor_mcu: mmu0
min_temp: 0
max_temp: 130

[temperature_sensor _Lane_1_onboard]
sensor_type: temperature_mcu
sensor_mcu: mmu1
min_temp: 0
max_temp: 130

[temperature_sensor _Lane_2_onboard]
sensor_type: temperature_mcu
sensor_mcu: mmu2
min_temp: 0
max_temp: 130

[temperature_sensor _Lane_3_onboard]
sensor_type: temperature_mcu
sensor_mcu: mmu3
min_temp: 0
max_temp: 130

[temperature_sensor _Lane_4_onboard]
sensor_type: temperature_mcu
sensor_mcu: mmu4
min_temp: 0
max_temp: 130

[temperature_sensor _Lane_5_onboard]
sensor_type: temperature_mcu
sensor_mcu: mmu5
min_temp: 0
max_temp: 130

[temperature_sensor _Lane_6_onboard]
sensor_type: temperature_mcu
sensor_mcu: mmu6
min_temp: 0
max_temp: 130

[temperature_sensor _Lane_7_onboard]
sensor_type: temperature_mcu
sensor_mcu: mmu7
min_temp: 0
max_temp: 130

# === Fans ===

[fan_generic _emu_fan_0]
pin: mmu0:MMU_FAN
max_power: 1
kick_start_time: 0.5

[fan_generic _emu_fan_1]
pin: mmu1:MMU_FAN
max_power: 1
kick_start_time: 0.5

[fan_generic _emu_fan_2]
pin: mmu2:MMU_FAN
max_power: 1
kick_start_time: 0.5

[fan_generic _emu_fan_3]
pin: mmu3:MMU_FAN
max_power: 1
kick_start_time: 0.5

[fan_generic _emu_fan_4]
pin: mmu4:MMU_FAN
max_power: 1
kick_start_time: 0.5

[fan_generic _emu_fan_5]
pin: mmu5:MMU_FAN
max_power: 1
kick_start_time: 0.5

[fan_generic _emu_fan_6]
pin: mmu6:MMU_FAN
max_power: 1
kick_start_time: 0.5

[fan_generic _emu_fan_7]
pin: mmu7:MMU_FAN
max_power: 1
kick_start_time: 0.5


# === MMU Fan Auto-Control (multi-sensor / multi-fan) ===
#
# Pairs each temperature sensor with a fan by index and controls
# that fan with hysteresis based on the paired sensor.
#
# Example:
#   variable_sensors: "Lane_0_onboard,Lane_0_onboard"
#   variable_fans:    "mmu_fan_0,mmu_fan_1"
#
# Notes:
# - Lists must be comma-separated names (no spaces, or strip spaces).
# - If list lengths differ, the shorter length is used (index pairing).
# - FORCE (below) is global: affects all listed fans.

[gcode_macro MMU_FAN_CFG]
description: Holds configuration/state for multi fan controller.
variable_on_temp: 39.0
variable_off_temp: 37.0
variable_poll_s: 5.0
variable_enabled: True
variable_forced: -1                 # -1=AUTO, 0=all OFF, 1=all ON (global)
variable_sensors: "_Lane_0_onboard,_Lane_1_onboard,_Lane_2_onboard,_Lane_3_onboard,_Lane_4_onboard,_Lane_5_onboard,_Lane_6_onboard,_Lane_7_onboard"   # Comma-separated temperature_sensor names
variable_fans:    "_emu_fan_0,_emu_fan_1,_emu_fan_2,_emu_fan_3,_emu_fan_4,_emu_fan_5,_emu_fan_6,_emu_fan_7"  # Comma-separated fan_generic names
variable_warned_len_mismatch: False # internal: warn once per enable
gcode:

[gcode_macro MMU_FAN_MONITOR_ENABLE]
description: Enable automatic multi-fan control.
gcode:
  SET_GCODE_VARIABLE MACRO=MMU_FAN_CFG VARIABLE=enabled VALUE=True
  UPDATE_DELAYED_GCODE ID=_MMU_FAN_LOOP DURATION=0.1
  RESPOND TYPE=echo MSG="MMU multi-fan monitor ENABLED"

[gcode_macro MMU_FAN_MONITOR_DISABLE]
description: Disable automatic control and switch all fans OFF.
gcode:
  SET_GCODE_VARIABLE MACRO=MMU_FAN_CFG VARIABLE=enabled VALUE=False
  UPDATE_DELAYED_GCODE ID=_MMU_FAN_LOOP DURATION=0
  {% set cfg = printer["gcode_macro MMU_FAN_CFG"] %}
  {% set fans = (cfg.fans|string).replace(' ','').split(',') %}
  {% for f in fans %}
    {% if f|length > 0 %}
      SET_FAN_SPEED FAN={f} SPEED=0.0
    {% endif %}
  {% endfor %}
  RESPOND TYPE=echo MSG="MMU multi-fan monitor DISABLED and all fans OFF"

[gcode_macro MMU_FAN_FORCE]
description: Global manual override for all configured fans.
# Usage:
#   MMU_FAN_FORCE S=1   -> Force ALL ON
#   MMU_FAN_FORCE S=0   -> Force ALL OFF
#   MMU_FAN_FORCE S=-1  -> Return to AUTO (per-sensor hysteresis)
gcode:
  {% set s = params.S|default(-1)|int %}
  {% if s not in [-1,0,1] %}
    RESPOND TYPE=error MSG="MMU_FAN_FORCE: S must be -1, 0, or 1"
  {% else %}
    SET_GCODE_VARIABLE MACRO=MMU_FAN_CFG VARIABLE=forced VALUE={s}
    {% set cfg = printer["gcode_macro MMU_FAN_CFG"] %}
    {% set fans = (cfg.fans|string).replace(' ','').split(',') %}
    {% if s == 1 %}
      {% for f in fans %}
        {% if f|length > 0 %}
          SET_FAN_SPEED FAN={f} SPEED=1.0
        {% endif %}
      {% endfor %}
      RESPOND TYPE=echo MSG="MMU fans FORCED ON"
    {% elif s == 0 %}
      {% for f in fans %}
        {% if f|length > 0 %}
          SET_FAN_SPEED FAN={f} SPEED=0.0
        {% endif %}
      {% endfor %}
      RESPOND TYPE=echo MSG="MMU fans FORCED OFF"
    {% else %}
      RESPOND TYPE=echo MSG="MMU fans returned to AUTO mode"
    {% endif %}
  {% endif %}

[delayed_gcode _MMU_FAN_LOOP]
initial_duration: 1
gcode:
  {% set cfg = printer["gcode_macro MMU_FAN_CFG"] %}
  {% if cfg.enabled %}
    {% set forced  = cfg.forced|int %}
    {% set on_t    = cfg.on_temp|float %}
    {% set off_t   = cfg.off_temp|float %}
    {% set sensors = (cfg.sensors|string).replace(' ','').split(',') %}
    {% set fans    = (cfg.fans|string).replace(' ','').split(',') %}
    {% set n_s     = sensors|length %}
    {% set n_f     = fans|length %}
    {% set n_min   = (n_s if n_s < n_f else n_f)|int %}

    {% if n_s != n_f and (not (cfg.warned_len_mismatch|default(False))) %}
      RESPOND TYPE=echo MSG={"MMU_FAN: sensor/fan list length mismatch"}
      SET_GCODE_VARIABLE MACRO=MMU_FAN_CFG VARIABLE=warned_len_mismatch VALUE=True
    {% endif %}

    {% if forced == 1 %}
      {% for i in range(0, n_min) %}
        {% set f = fans[i] %}
        {% if f|length > 0 %}
          SET_FAN_SPEED FAN={f} SPEED=1.0
        {% endif %}
      {% endfor %}
    {% elif forced == 0 %}
      {% for i in range(0, n_min) %}
        {% set f = fans[i] %}
        {% if f|length > 0 %}
          SET_FAN_SPEED FAN={f} SPEED=0.0
        {% endif %}
      {% endfor %}
    {% else %}
      {% for i in range(0, n_min) %}
        {% set s_name = sensors[i] %}
        {% set f = fans[i] %}
        {% if s_name|length > 0 and f|length > 0 %}
          {% set t = printer["temperature_sensor " ~ s_name].temperature|float %}
          {% set cur_speed = (printer["fan_generic " ~ f].speed|default(0.0))|float %}
          {% set cur_state = 1 if cur_speed >= 0.5 else 0 %}
          {% if cur_state == 0 %}
            {% set target_state = 1 if t >= on_t else 0 %}
          {% else %}
            {% set target_state = 1 if t > off_t else 0 %}
          {% endif %}
          {% if target_state != cur_state %}
            {% if target_state == 1 %}
              SET_FAN_SPEED FAN={f} SPEED=1.0
            {% else %}
              SET_FAN_SPEED FAN={f} SPEED=0.0
            {% endif %}
          {% endif %}
        {% endif %}
      {% endfor %}
    {% endif %}

    UPDATE_DELAYED_GCODE ID=_MMU_FAN_LOOP DURATION={cfg.poll_s}
  {% endif %}

# Happy Hare LED additions

[mmu_led_effect mmu_static_white_dim]
define_on:    gates
layers:       static 0 0 top (0.3,0.3,0.3)

[mmu_led_effect mmu_ready_white]
define_on:    gates
layers:       breathing 2 0 subtract (0.4,0.4,0.4)
              static 0 0 top (0.5,0.5,0.5)

[mmu_led_effect mmu_ready_red]
define_on:    gates
layers:       breathing 2 0 subtract (0.4,0.0,0.0)
              static 0 0 top (0.5,0.0,0.0)
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

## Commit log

2025-10-26 Improve printability of box_base wiring hatch and updated built-in support
2025-10-27 Added custom LED effects
2025-11-10 EMU Sync Assembly Images
2025-12-02 base update: Heatsets for electronics mounting points
    [[a]_Ebb36_Mount.stl, [a]_Ebb42_Mount.stl]
2025-12-31 Small changes to PSF EMUSync assembly and parts * Shortened EMUSync main EMUSync_main_body[PSF].stl * Adjusted indicator marks on main EMUSync_main_body[PSF].stl * Adjusted depth of PTFE Cutter and L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
    [EMUSync_main_body[PSF].stl, PTFE Cutter and Length Tool[PSF].stl, [a]_End_cap[PSF].stl]
2026-01-04 Update hardware pin definitions to remove unnecessary numbering
2026-01-09 Revert hardware i2c bus change (use software i2c bus) for BME sensors
    To combat occasional i2c timeout errors
    [emu_macros.cfg]
2026-01-09 Revert hardware i2c change in documentation
2026-01-19 PCB text and license updates. Credits added.
2026-01-22 Add patched AHT10 and BME280 klipper files
2026-01-24 fix pin alias in fan macros
    [emu_macros.cfg]
2026-01-27 Updated filamentalist assembly video errata.
2026-02-03 Add PCB Hatch wiring dimensions
2026-02-03 Fix link to Base wiring dimensions
2026-02-03 Add wire lengths for old PCB board
2026-02-03 Fix dimensions for DIY Hatch
    - Increase length of led wires from 120mm to 150mm
    - Increase length for BME sensor from 140 to 150mm
    - Increase length of entry sensor from 120 to 140mm
    - Increase length of post extruder sensor from 140mm to 160mm
2026-02-03 Fix wiring dimension for stepper
2026-02-03 Update alignment of DIY Hatch wires
2026-02-03 Fix dimensions for DIY Hatch (#12)
    * Fix dimensions for DIY Hatch
    * Fix wiring dimension for stepper
    * Update alignment of DIY Hatch wires
    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
2026-02-04 EMU Base wiring - Update pigtail motor jst diagram (#14)
    Update wording for the stepper wires

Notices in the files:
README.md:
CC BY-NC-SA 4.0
